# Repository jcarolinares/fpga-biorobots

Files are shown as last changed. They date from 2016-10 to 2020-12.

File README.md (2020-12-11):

# FPGA- BIOROBOTS

## Hybrid bio-inspired architecture for robots using open source FPGAs.

Animal nervous system             |  Bio-inspired robot nervous system
:-------------------------:|:-------------------------:
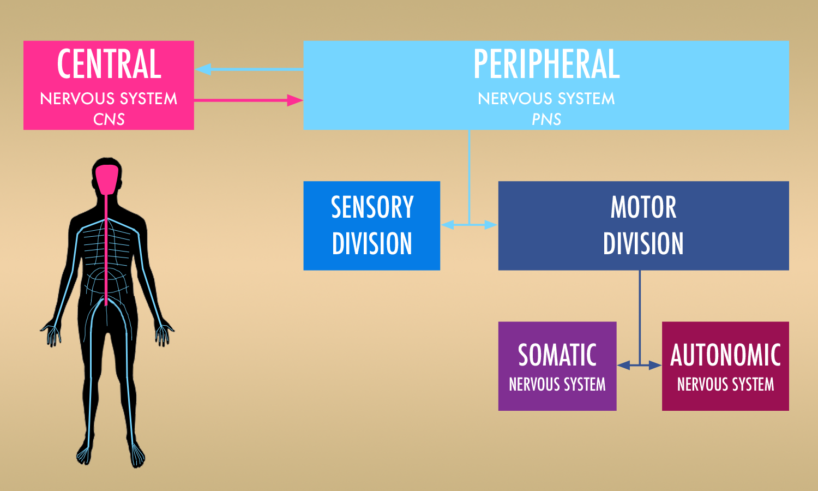
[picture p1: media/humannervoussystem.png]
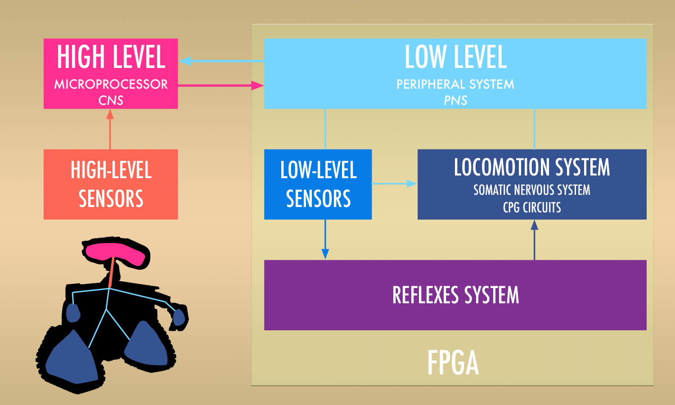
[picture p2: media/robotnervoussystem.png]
  |  

:gb: A robotic control architecture inspired in the animal nervous system that combines the use of microcomputers as the brain with the use of Open Source FPGAs as the nervous system.

Here you can find all the publications, material, robots, tools, circuits and programs developed for my master thesis work at Universidad Politécnica de Madrid.

***

:es: Repositorio con el material generado para mi trabajo de fin de Master de Robótica y Automática por la Universidad Politécnica de Madrid sobre el desarrollo de una arquitectura de control robótica híbrida y bioinspirada combinando microprocesadores y FPGAs libres.

***
## Publications

### IROS 2018 Paper

Part of this project has been published at **_2018 IEEE/RSJ International Conference on Intelligent Robots and Systems_** or **_IROS 2018_** with the title:

_"Hybrid Bio-Inspired Architecture for Walking Robots Through Central Pattern Generators Using Open Source FPGAs"_

https://ieeexplore.ieee.org/abstract/document/8594288

You can cite this article on bibtex with:

```
@inproceedings{linares2018hybrid,
  title={Hybrid bio-inspired architecture for walking robots through Central Pattern Generators using open source FPGAs},
  author={Linares, Juli{\'a}n Caro and Barrientos, Antonio and M{\'a}rquez, Enric Mayas},
  booktitle={2018 IEEE/RSJ International Conference on Intelligent Robots and Systems (IROS)},
  pages={7071--7076},
  year={2018},
  organization={IEEE}
}
```

### Master Thesis Memory

You can read and download the memory document of this Master Thesis project here:

https://github.com/jcarolinares/fpga-biorobots/blob/final-revision-cleaning/Thesis%20Memory/MasterThesis-BioInspiredrobotsOpenSourceFPGAs.pdf

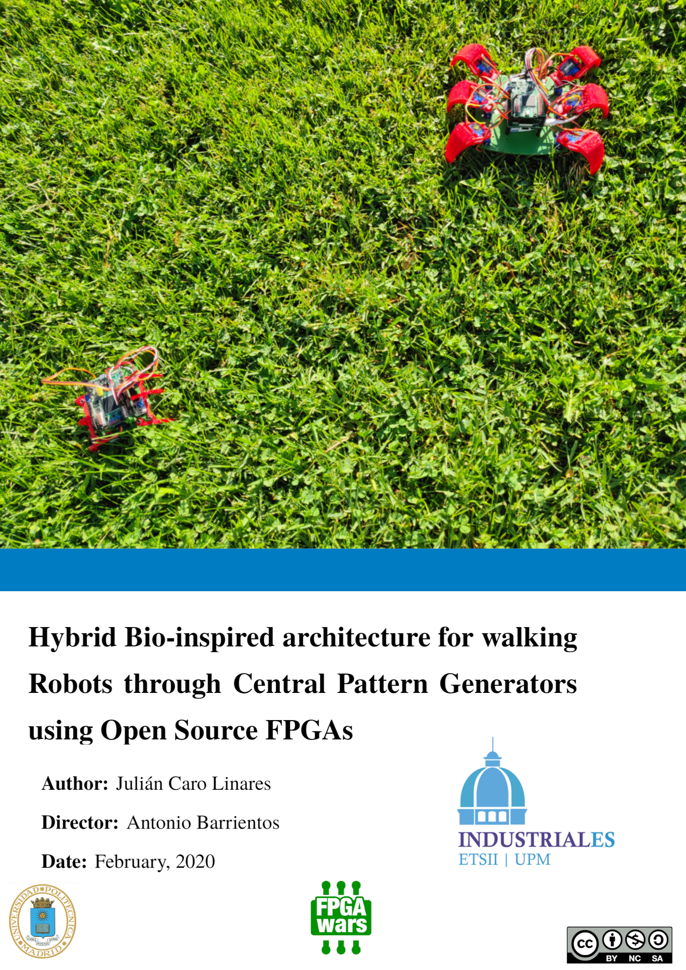
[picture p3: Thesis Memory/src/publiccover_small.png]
Master Thesis cover


You can cite this article on bibtex with:

```
@mastersthesis{fpgabiorobots2020,
  title={Hybrid bio-inspired architecture for walking robots through Central Pattern Generators using open source FPGAs},
  author={Linares, Juli{\'a}n Caro},
  school={Universidad Polit{\'e}cnica de Madrid},
  year={2020}
}
```

***

<br /><span xmlns:dct="http://purl.org/dc/terms/" property="dct:title">FPGA-Biorobots</span> by <span xmlns:cc="http://creativecommons.org/ns#" property="cc:attributionName">Julián Caro Linares</span> licensed by <a rel="license" href="http://creativecommons.org/licenses/by-sa/4.0/">Creative Commons Attribution-ShareAlike 4.0 International License</a>.<br /><br />

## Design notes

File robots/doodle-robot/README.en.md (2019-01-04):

# Doodle- Assembly instructions

  

**Read this in other languages:** :es: [Spanish](README.md)

**Some videos of Doodle**

<a href="http://www.youtube.com/watch?feature=player_embedded&v=VI5Jhr64cQY
" target="_blank">Basic video</a>
<a href="http://www.youtube.com/watch?feature=player_embedded&v=HQzxtiUjpWk
" target="_blank">Normal VS Triangular oscillators movement</a>   <a href="http://www.youtube.com/watch?feature=player_embedded&v=YqtSMF6W4vM
  " target="_blank">Line follower</a>
  <a href="http://www.youtube.com/watch?feature=player_embedded&v=JEpjGYJFocM
  " target="_blank">Fake slow motion movement</a>
  <a href="http://www.youtube.com/watch?feature=player_embedded&v=NQqp7YjglOo
  " target="_blank">Line follower using oscillators</a>
  <a href="http://www.youtube.com/watch?feature=player_embedded&v=UbCZ-bBiaz4o
  " target="_blank">Triangular oscillator VS Sine oscillators</a>
<br><br>

Here you have a step by step guide to assemble the Doodle robot. Doodle is a very simple robot and its building shouldn't take more than 30 minutes.

## Materials

### Electronic

* 1x-Icezum Alhambra, Arduino UNO or an equivalent board.

* 3x-Micro small micro servomotors of the family SG90R. In the original robot I've used ** SG92R ** servomotors. You will versions of the legs for the SG90 servomotors and SG92.

* [Optional] 2x-Lipo batteries: 3.7 V 240 mAh + Compatible charger. There are many options on the internet, an example:

  http://www.dx.com/p/502030-240mah-rechargeable-polymer-li-ion-battery-silver-227107

* [Optional] Additional sensors or servomotors. In the front part of the robot there's two general purpose holes where you can add sensors of a Educational robotis kits (Example: bq sensors) or two servomotors

### Screws and servomotors horns

You'll need **M3 and M2 screws and nuts**, also the small screws that come with the servomotors. The long of each screw is not important so you'll could build the robot using any M3 or M2 screw that you have.

* 4x-Screws M2x10

* 1x-Screw M2x15 or similar

* 8x-Screws M3x8

* 4x-Screws M3x25 [2 Optional-Battery holder]

* Screws and horns included with the servomotors.

* 1x-Double horn

* 2x-Single horn

### 3D parts

You'll need to print:

* 1x-Front left leg

* 1x-Front right leg

* 1x-Back left leg

* 1x-Back right leg

* 1x- Central leg

* 2x Leg links

* 1x base

* [Opcional] 1x- Battey holder

* [Opcional] 2x- Googly eyes

***
## Assembly step by step

**1-** Put the two servomotors in the back holes of the robot using M2x10 screws and nuts.

  

**2-** Carefully, insert the M3 nut inside each leg, depending of your 3D printer quality you'll need to push the nuts with a little pressure, even heating up the nuts a little bit

  

  **Tip:**

  It is not essential but you can put a bit of silicone at the end of the legs using a hot melt gun. Your robot will have a better adhesion to the surface.

  

**3-** Insert the single horns in each leg and attach them to the servomotors. Althought you can fix it later without problems, **is important** that at this moment you can try to put the legs on the servos in order to have an amplitude of 90 degrees backwards and forward. The position where the legs are perpenticular to the base has to be 90 degrees on your servo. You can create a simple program for this purpose. Screw the legs to the servomotors.

     

**4-** If you are going to put some sensors or additional servomotors in the front holes it's  the right time to do it. Use M3 Screws and nuts for the sensors and M2 for the servomotors.

  

  **Tip:**

  If you are going to use the battery holder, screw it only the sensors screws near the outside of the base, leave the central holes empty.

**5-** Screw the front legs in the front holes using M3 screws and nuts. Keep in mind that the leg has to turn free so don't tight it up too much. If you are going to use the battery holder, use longer screws like M3x18.

  

**6-** Screw the leg links on the legs. The bug hairs have to be at the outside . Use M3x8 and remember to let that the legs can move free.

  

**7-** Put the double horn in the central leg. Attach the leg to the servomotor keeping in mind that the 90º degrees position will be the neutral position of the leg.

  

**8.** Fit the central servomotor in the base using a long M2 screw and a nut.

  

**9-** Attach your FPGA Icezum Alhmabra or Arduino UNO board (or similar) on the columns using M3 screws.

  

  **Tip:**

  Before the board attachment

  Before placing the board, make sure that your cables pass through the central area of the robot at the rear, between the two servos.

  

**10-** Customize your robot putting a pair of googly eyes in the front.

Doodle is ready!

  

***
[Optional-Battery holder]

In the case you wish to use the battery holder you'll have to use long M3x18 screws in the step 5.



***

<br /><span xmlns:dct="http://purl.org/dc/terms/" property="dct:title">Doodle </span> by <span xmlns:cc="http://creativecommons.org/ns#" property="cc:attributionName">Julián Caro Linares</span> licensed by <a rel="license" href="http://creativecommons.org/licenses/by-sa/4.0/">Creative Commons Attribution-ShareAlike 4.0 International License</a>.<br /><br />

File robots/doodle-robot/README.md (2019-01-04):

# Doodle- Instrucciones de montaje

  

**Read this in other languages:** [English](README.en.md)

**Algunos vídeos en funcionamiento**

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

Aquí tienes una guía paso a paso para montar a Doodle. Doodle es un robot muy sencillo por lo que su montaje no debería llevarte más de media hora.

## Materiales

### Electrónica

* 1x-Icezum Alhambra, Arduino UNO o placa equivalente.

* 3x-Micro servomotores pequeños de la familia SG90R. En el robot original se han usado servomotores **SG92R** por lo que encontrarás patas para las dos versiones: SG90 y SG92R.

* [Opcional] 2x-Baterías lipo 3.7 V 240 mAh + Cargador compatible. Existen muchas baterías lipo de este tipo. Un ejemplo:

  http://www.dx.com/p/502030-240mah-rechargeable-polymer-li-ion-battery-silver-227107

* [Opcional] Sensores o servomotores adicionales. En la parte delantera del robot hay dos hendiduras donde pueden agregarse sensores de kits de robótica tipo bq zum o similares o dos servomotores.

### Tornillos y cabezales de servomotor

Necesitarás tornillos de **métrica M3 y M2** así como **los tornillos que vienen con los servomotores**. Los **tamaños** de cada tornillo **no son excesivamente importantes** por lo que podrás realizar el montaje con cualquier tornillo de las métricas M2 o M3 que tengas a mano.

* 4x-Tornillos M2x10

* 1x-Tornillo M2x15 o similar

* 8x-Tornillos M3x8

* 4x-Tornillos M3x25 [2 Opcionales-Portabaterías]

* Tornillos y cabezales incluidos con los servos.

* 1x-Cabezal doble

* 2x-Cabezal simple

### Piezas 3D

Necesitarás imprimir:

* 1x-Pata delantera izquierda

* 1x-Pata delantera derecha

* 1x-Pata trasera izquierda

* 1x-Pata trasera derecha

* 1x- Pata central

* 2x Links de patas

* 1x base

* [Opcional] 1x-Portabaterias

* [Opcional] 2x-Ojitos saltones

***
## Montaje paso a paso

**1-** Introduce los dos servomotores en su hueco de la parte trasera del robot. Atorníllalos con tornillos y tuercas M2x10

  

**2-** Con cuidado, introduce la tuerca en las patas traseras Dependiendo de tu impresora y calibración tendrás que introducir las tuercas con un poco de presión o incluso aplicando calor. Coloca también el *horn* de un solo brazo dentro de la pata, introduciéndolo a presión hasta que que su lado posterior quede dentro de la pata.

  

  **Consejo:**

  Aunque no es imprescindible,  para hacer que tu robot tenga más adhesión puedes poner un poco de silicona en sus patas utilizando una pistola de termofusible. Procura que el pegote que pegues no sea demasiado grande y quede plano sobre la pata.

  

**3-** Introduce los *horns* de un solo brazo en cada pata y coloca las patas sobre los servomotores. Aunque más tarde podrás corregirlo sin problemas, **es importante** que ahora intentes colocar las patas en los servos de forma que tengan una amplitud de movimientos de hasta 90 grados hacia atrás y chocando con la base hacia delante, siendo el ángulo 90º el perpenticular a la base. Para ello puedes incluso crear un pequeño programa donde pongas tus servos a 90º y aprovecha para atornillarlos.

     

**4-** Si vas a colocar algún sensor o servo adicional en las ranuras delanteras, es un buen momento para hacerlo. Utiliza tornillos y tuercas M3 para los sensores y tornillos y tuercas M2 para los servomotores.

  

  **Consejo:**

  En el caso de que vayas a colocar el portabaterias inferior, atornilla solo los tornillos de los sensores de la parte exterior, deja los agujeros centrales sin atornillar.     

**5-** Atornilla las patas delanteras en los agujeros de delante utilizando tornillos y tuercas M3. Recuerda que la pata debe poder girar libremente, por lo que no la aprietes demasiado . Puedes usar tornillos M3x10 o inferiores si no vas a colocar un portabaterias en la zona inferior, o utilizar tornillos M3x18 en caso afirmativo.

  

**6-** Atornilla los links o transmisores de movimiento sobre las patas. Los pelos del insecto deben quedar en la parte exterior del robot. Utiliza tornillos M3x8 y recuerda apretar bien pero permitiendo el movimiento de las patas.

  

**7-** Coloca el *horn* doble en la pata grande central. Atornilla la pata al servomotor recordando que la posición 90 grados será la posición natural de la pata, totalmente horizontal.

  

**8-** Encaja el servomotor central en la base situada en la parte delantera. Aseguralo utilizando un tornillo largo y una  tuerca M2.

  

**9-**  Coloca tu FPGA Icezum Alhambra o una placa Arduino Uno o equivalente, atornillándola con tornillos M3 en las columnas delanteras del robot.

  

  **Consejo:**

  Antes de colocar la placa procura que tus cables pasen por la zona central del robot en la parte trasera, situándose entre ambos servos.

  

**10-** Decora tu robot colocándole un par de ojitos saltones en la parte delantera.

  ¡Doodle está listo para la acción!

      

***
[Opcional-Portabaterías]

En el caso de que desees colocar el portabaterias deberás utilizar tornillos largos M3x18 o más en la zona en el paso 5 con sus respectivas tuercas en la parte inferior.



***

<br /><span xmlns:dct="http://purl.org/dc/terms/" property="dct:title">Doodle </span> por <span xmlns:cc="http://creativecommons.org/ns#" property="cc:attributionName">Julián Caro Linares</span> licensed by <a rel="license" href="http://creativecommons.org/licenses/by-sa/4.0/">Creative Commons Attribution-ShareAlike 4.0 International License</a>.<br /><br />

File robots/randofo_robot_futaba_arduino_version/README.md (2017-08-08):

# Randofo-Arduino and Futaba 3003 Version

  

  **A video of Randofo controlled with oscillators and an open source FPGA**

  <center><a href="http://www.youtube.com/watch?feature=player_embedded&v=ET-EtgHS6wI
  " target="_blank">Time to meal video</a></center><br><br>

This is Randofo. A very cool and simple robot created by Randy Sarafan (His nick is Randofo in Instructables)

You can find the original version here:

http://www.instructables.com/id/3D-Printed-Robot/

The original project uses Standar Servos from Radioshack. I created my own version of the body to use **futaba 3003 motors or similar and Arduino UNO or similar boards**

I also created a hardware control using Icestudio and the Icezum Alhambra, an open source FPGA board.

More info at: https://github.com/FPGAwars?page=1

## Materials

### Miscellaneous

* 4x Pencils

**At least two of them must have erasers**

### Electronics

* 2x-Futaba 3003 servomotors or similar

* 1x-Arduino UNO board or similar. In my case I used an Icezum Alhambra FPGA board.

* Batteries-Depends of your board and motors. But you can feed the robot using two Lipo batteries of 3.7V or a Powerbank.

### Screws

* 2x-Servo screws- The screws that comes with the servomotors.

* 12x Screws M3x12 or similar.

* 12 M3 nuts.

### 3D-Parts

* 1x-randofo_body

* 1x-gear

* 1x-back_legs

* 1x-left_leg

* 1x-right_leg

The legs and gears are easy to print but you'll probably need supports.

The body due to his form, however, will need more supports and time. If you are using Cura I recommend to change the Line Support distance to 3.6667 for a better support removement.  

***
## Assembly

I reccomend to follow the original instructions of instructables:

http://www.instructables.com/id/3D-Printed-Robot/

The only difference is the electronic part. In this version you directly have the PCB holes for Arduino UNO or similar.

***

## Programming

* In the case of an Arduino, you can use the original Arduino code. It's simple but it works!

* In the case that you are using an Icezum Alhambra FPGA board you have the hardware in the format of an Icestudio file. You can easily change the values of the roms that controls the servomotor movements using the program *oscillator_rom_generator.py*

You can download Icestudio here:

https://github.com/FPGAwars/icestudio

***

<br /><span xmlns:dct="http://purl.org/dc/terms/" property="dct:title">Randofo. A simple robot controlled with an Open Source FPGA</span> by <span xmlns:cc="http://creativecommons.org/ns#" property="cc:attributionName">Julián Caro Linares</span> licensed by <a rel="license" href="https://creativecommons.org/licenses/by-nc-sa/4.0/">Creative Commons Attribution-Non comercial-ShareAlike 4.0 International License</a>.<br /><br />

Based on <a xmlns:dct="http://purl.org/dc/terms/" href="http://www.instructables.com/id/3D-Printed-Robot/" rel="dct:source">http://www.instructables.com/id/3D-Printed-Robot/</a>

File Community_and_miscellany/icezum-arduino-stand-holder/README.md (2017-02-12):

# ICEzum-Arduino Stand holder



This is a simple Arduino and derivatives stand holder. I made two version, a piece where you can put your board in vertical or horizontal, and a piece with a inclination of 30 degrees to proudly show and use your board.

I made this model for the open source FPGA IceZum Alhambra, but is compatible with any Arduino UNO shape board.

You can find more info about the Icezum Alhambra at FPGAWars:

https://github.com/FPGAwars?page=1

=============

<br /><span xmlns:dct="http://purl.org/dc/terms/" property="dct:title">ICEzum-Arduino Stand holder</span> by <span xmlns:cc="http://creativecommons.org/ns#" property="cc:attributionName">Julián Caro Linares</span> licensed by <a rel="license" href="http://creativecommons.org/licenses/by-sa/4.0/">Creative Commons Attribution-ShareAlike 4.0 International License</a>.<br /><br />

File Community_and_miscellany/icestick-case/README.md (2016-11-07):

#ICEstick Case



Modified design based on the original of Juan Gonzalez Gomez:

<a href="https://github.com/Obijuan/3D-parts/tree/master/2015-12-23-icestick-case">https://github.com/Obijuan/3D-parts/tree/master/2015-12-23-icestick-case</a>

Changes respect the original:

- Optional screws supports out of the case.

- Slightly enlargement of some tolerances.

- <a href="https://github.com/FPGAwars?page=1">FPGAWars Logo </a>and ICEstick text added.

=============

<br /><span xmlns:dct="http://purl.org/dc/terms/" property="dct:title">ICEstick case</span> por <span xmlns:cc="http://creativecommons.org/ns#" property="cc:attributionName">Julián Caro Linares based on the design of Juan Gonzalez Gomez</span> licensed by <a rel="license" href="http://creativecommons.org/licenses/by-sa/4.0/">Creative Commons Attribution-ShareAlike 4.0 International License</a>.<br /><br />

Based on <a xmlns:dct="http://purl.org/dc/terms/" href="https://github.com/Obijuan/3D-parts/tree/master/2015-12-23-icestick-case" rel="dct:source">https://github.com/Obijuan/3D-parts/tree/master/2015-12-23-icestick-case</a>

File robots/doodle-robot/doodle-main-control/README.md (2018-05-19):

# Doodle brain

(WIP)

The main brain module or high level module of Doodle

This modules is able of create the low level circuits of the robots in and upload them to the FPGA in real time.

The brain can be excuted in a Raspberry pi 2 or 3 with apio installed.

Actually **is NOT compatible** with Raspberry zero due to Apio and an incompatibility between architectures.

## To correctly test this program you will need:

* Python 3

* Apio:

  ``` bash
  sudo pip3 install apio
  ```

* Empy:

 ``` bash
 sudo pip3 install empy
 ```
* Python 3 tk:

  ``` bash
  sudo apt-get install python3-tk
  ```

* Matplotlib:

  ``` bash
  sudo pip3 install matplotlib
  ```

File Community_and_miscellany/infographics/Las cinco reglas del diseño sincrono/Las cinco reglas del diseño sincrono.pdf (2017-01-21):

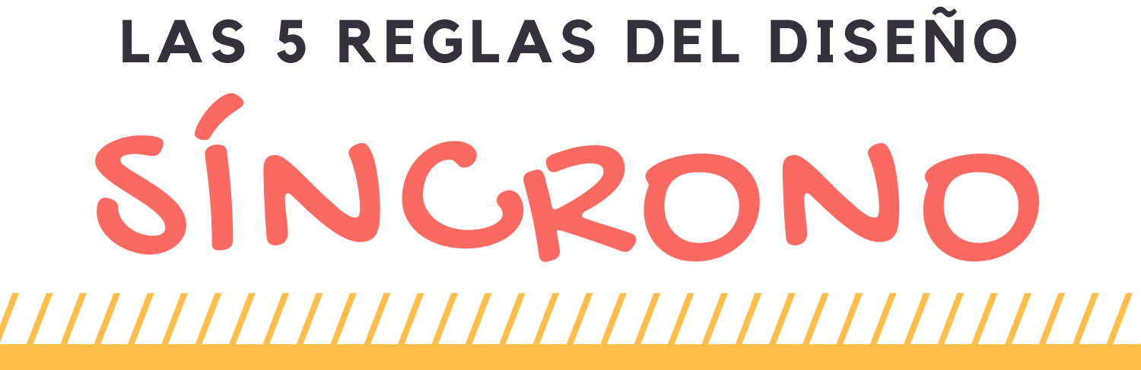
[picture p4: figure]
SÍNCRONO; LAS 5 REGLAS DEL DISEÑO

## UN ÚNICO RELOJ PARA GOBERNARLOS A TODOS

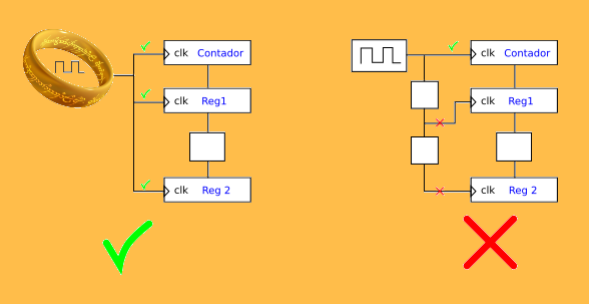
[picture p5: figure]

TODAS las entradas de reloj se deben conectar directamente a un único reloj, común a todos.

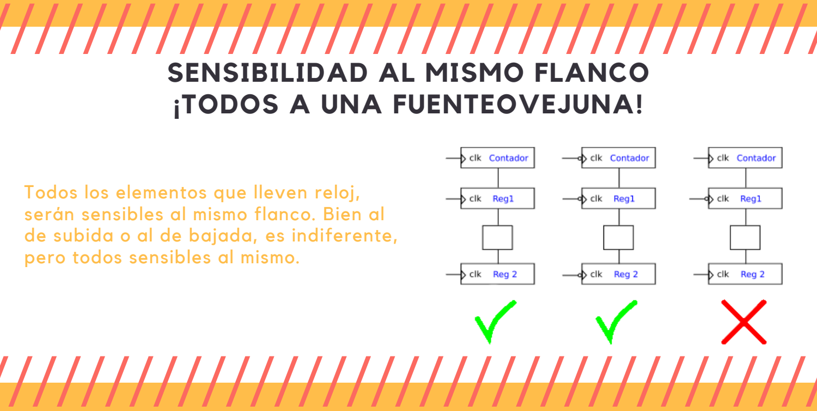
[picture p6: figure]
Todos los elementos que lleven reloj,; pero todos sensibles al mismo.; SENSIBILIDAD AL MISMO FLANCO ¡TODOS A UNA FUENTEOVEJUNA!

serán sensibles al mismo flanco. Bien al de subida o al de bajada, es indiferente,

## ANTES DE ENTRAR A UN CIRCUITO COMBINACIONAL PASE POR REGISTRO POR FAVOR

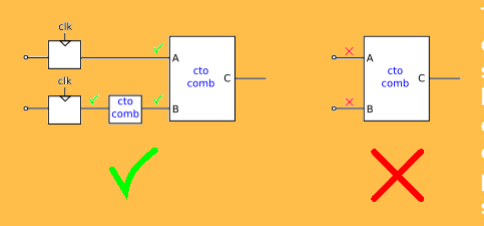
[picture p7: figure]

Todas las entradas de los circuitos combinacionales deben estar conectadas a salidas de circuitos secuenciales, sincronizadas con el reloj del sistema, o bien a otros circuitos combinacionales que cumplan esta regla. Es decir, que cualquier entrada de un circuito combinacional tiene que ser capturada antes por un registro. Las entradas que cumplen esta regla

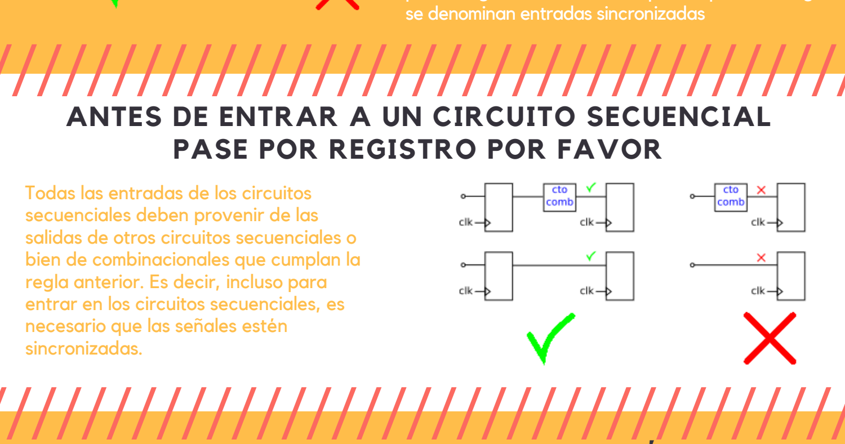
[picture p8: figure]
se denominan entradas sincronizadas; PASE POR REGISTRO POR FAVOR; Todas las entradas de los circuitos secuenciales deben provenir de las; bien de combinacionales que cumplan la regla anterior. Es decir, incluso para; necesario que las señales estén sincronizadas.

## ANTES DE ENTRAR A UN CIRCUITO SECUENCIAL

salidas de otros circuitos secuenciales o

entrar en los circuitos secuenciales, es

## SALIDAS DE UN COMBINACIONAL: SÓLO A ENTRADAS DE OTRO COMBINACIONAL, ENTRADAS SÍNCRONAS O SALIDAS DEL CIRCUITO SÍNCRONO

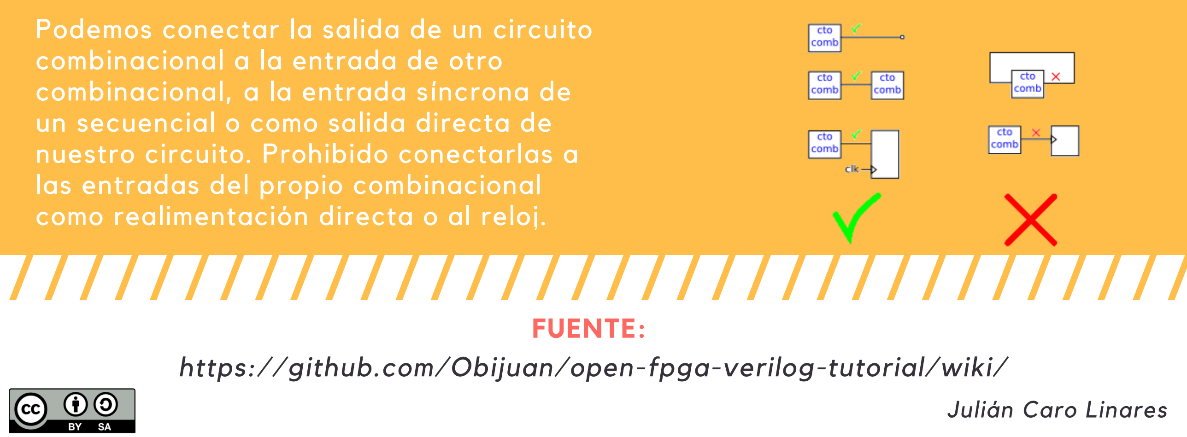
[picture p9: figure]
combinacional a la entrada de otro combinacional, a la entrada síncrona de un secuencial o como salida directa de nuestro circuito. Prohibido conectarlas a las entradas del propio combinacional como realimentación directa o al reloj.; FUENTE: https://github.com/Obijuan/open-fpga-verilog-tutorial/wiki/; Julián Caro Linares

Podemos conectar la salida de un circuito

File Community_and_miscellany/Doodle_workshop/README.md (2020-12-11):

# Doodle - Workshop

Materials of the workshop made at the [Maker Faire Oshwdem 2018.](https://oshwdem.org/2018/10/ultimos-talleres-antes-de-la-oshwdem-2018/)

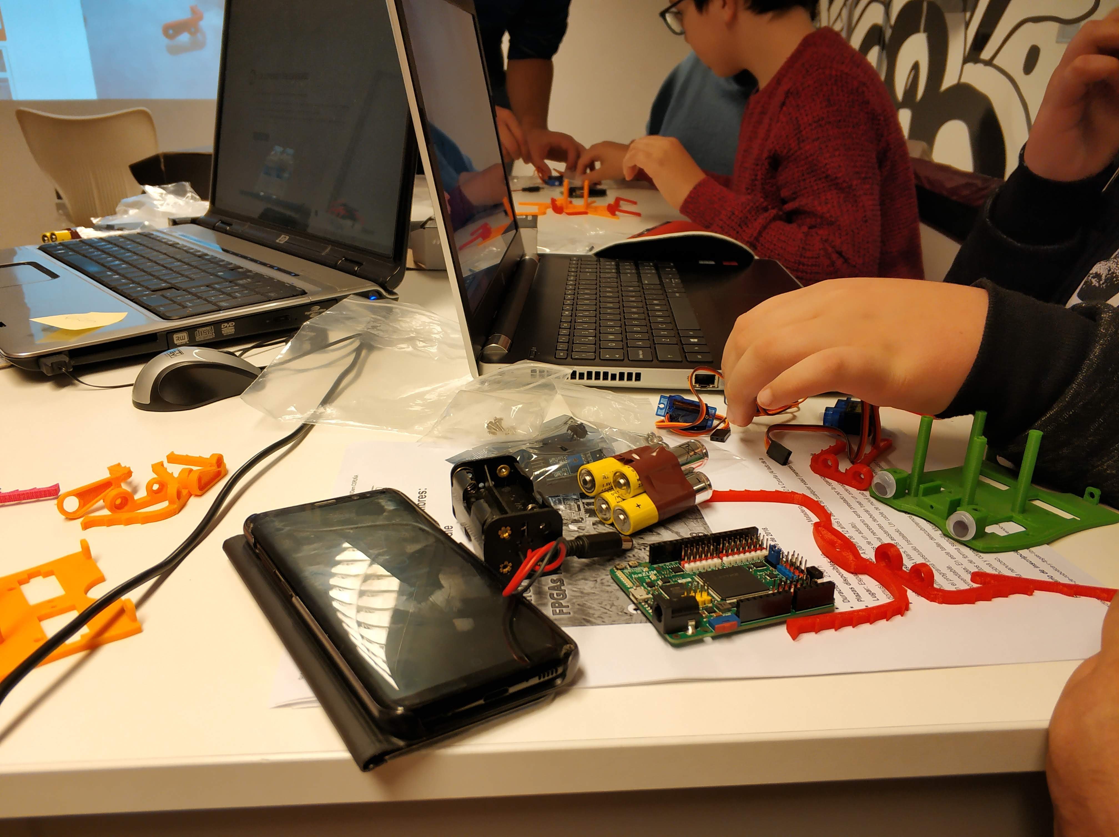
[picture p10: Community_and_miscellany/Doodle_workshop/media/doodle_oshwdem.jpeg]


The workshop, despite some problems, was so fun to do. More of the little improvements that Doodle has now were discover at this workshop.

Thank you to Nuria and Enrique and all the Oshwdem organization for their amazing help!

***

<br /><span xmlns:dct="http://purl.org/dc/terms/" property="dct:title">Doodle workshop</span> by <span xmlns:cc="http://creativecommons.org/ns#" property="cc:attributionName">Julián Caro Linares</span> licensed by <a rel="license" href="http://creativecommons.org/licenses/by-sa/4.0/">Creative Commons Attribution-ShareAlike 4.0 International License</a>.<br /><br />

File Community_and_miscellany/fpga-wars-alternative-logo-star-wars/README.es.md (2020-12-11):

# FPGA WARS: LOGO ALTERNATIVO STAR WARS

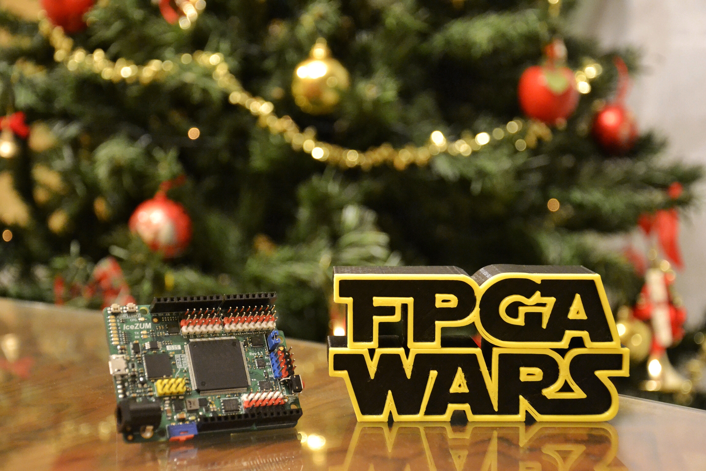
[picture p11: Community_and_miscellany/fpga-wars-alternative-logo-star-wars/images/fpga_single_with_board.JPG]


**Read this in other languages:** :gb: [English](README.md)

Repositorio con los archivos para imprimir, asi como los archivos fuente utilizados para la creación de un logo alternativo de la comunidad FPGA WARS, más información en:

- <a href="https://github.com/FPGAwars?page=1">Proyecto FPGA Wars</a>

- <a href="https://groups.google.com/forum/#!forum/fpga-wars-explorando-el-lado-libre">Comunidad FPGA Wars</a>

¡Gracias a la comunidad por su inestimable apoyo!

PD: ¿Buscas el logo de Star Wars?, pueden encontrarlo en: https://www.thingiverse.com/thing:2006957

***

<br /><span xmlns:dct="http://purl.org/dc/terms/" property="dct:title">FPGA Wars Logo Alternativo</span> por <span xmlns:cc="http://creativecommons.org/ns#" property="cc:attributionName">Julián Caro Linares</span> licensed by <a rel="license" href="http://creativecommons.org/licenses/by-sa/4.0/">Creative Commons Attribution-ShareAlike 4.0 International License</a>.<br /><br />

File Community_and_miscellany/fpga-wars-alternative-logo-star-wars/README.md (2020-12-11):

# FPGA WARS: ALTERNATIVE STAR WARS LOGO



**Read this in other languages:** :es: [Spanish](README.es.md)

Repository with the printing and source files of this alternative logo based on Star Wars for the open-source FPGA community FPGA WARS. More info at:

- <a href="https://github.com/FPGAwars?page=1">FPGA WARS project</a>

- <a href="https://groups.google.com/forum/#!forum/fpga-wars-explorando-el-lado-libre">FPGA WARS Community</a>

Thanks to the community for their unvaluable support!

PD: Are you looking for the original Star Wars logo? You can find it here: https://www.thingiverse.com/thing:2006957

***

<br /><span xmlns:dct="http://purl.org/dc/terms/" property="dct:title">FPGA Wars Alternative Logo</span> by <span xmlns:cc="http://creativecommons.org/ns#" property="cc:attributionName">Julián Caro Linares</span> licensed by <a rel="license" href="http://creativecommons.org/licenses/by-sa/4.0/">Creative Commons Attribution-ShareAlike 4.0 International License</a>.<br /><br />

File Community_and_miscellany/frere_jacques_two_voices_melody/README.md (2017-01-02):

#Frère Jacques Two voices melody

Melody created in Verilog following the tutorial example of Juan Gonzalez Gomez:

<a href="https://github.com/Obijuan/open-fpga-verilog-tutorial/wiki/Cap%C3%ADtulo-19%3A-Secuenciando-notas">https://github.com/Obijuan/open-fpga-verilog-tutorial/wiki/Cap%C3%ADtulo-19%3A-Secuenciando-notas</a>

If you have an IceZum Alhambra connect the first Buzzer to Pin 0 (119) and the second buzzer to Pin 1 (118)

If you are going to use another board, remember to change the PCF file connections.

=============

<br /><span xmlns:dct="http://purl.org/dc/terms/" property="dct:title">Frère Jacques Two voices melody</span> por <span xmlns:cc="http://creativecommons.org/ns#" property="cc:attributionName">Julián Caro Linares</span> licensed by <a rel="license" href="http://creativecommons.org/licenses/by-sa/4.0/">Creative Commons Attribution-ShareAlike 4.0 International License</a>.<br /><br />

Based on <a xmlns:dct="http://purl.org/dc/terms/" href="https://github.com/Obijuan/open-fpga-verilog-tutorial/wiki/Cap%C3%ADtulo-19%3A-Secuenciando-notas" rel="dct:source">https://github.com/Obijuan/open-fpga-verilog-tutorial/wiki/Cap%C3%ADtulo-19%3A-Secuenciando-notas</a>

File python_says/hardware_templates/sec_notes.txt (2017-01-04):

//--Fichero secnotas.v

//-- Incluir las constantes del modulo del divisor
`include "divider.vh"

//--Parametros

module secnotas(input wire clk, output reg ch_out, output reg ch_out2);

//--Notas a tocar
//--Definidas como parametros para las pruebas del testbench

parameter N0  = `DO_$octave;
parameter N1  = `RE_$octave;
parameter N2  = `MI_$octave;
parameter N3  = `FA_$octave;
parameter N4  = `SOL_$octave;
parameter N5  = `LA_$octave;
parameter N6  = `SI_$octave;
parameter N7  = `DO_$next_octave;

parameter DUR  = `T_${duration}ms;

//--Cables de salida de los canales

wire ch0, ch1, ch2,ch3,ch4,ch5,ch6,ch7;

//--Seleccion del canal del multiplexor
reg [5:0] sel=0;
reg [5:0] sel2=60;//Un compas retrasado

//-Reloj de duracion de la nota
wire clk_dur;

//--Canal 0
divider #(N0)
  CH0(
    .clk_in(clk),
    .clk_out(ch0)
  );

  //-- Canal 1
divider #(N1)
  CH1 (
      .clk_in(clk),
      .clk_out(ch1)
    );

  //-- canal 2
divider #(N2)
  CH2 (
      .clk_in(clk),
      .clk_out(ch2)
    );

//-- canal 3
divider #(N3)
  CH3 (
    .clk_in(clk),
    .clk_out(ch3)
  );

  //-- canal 4
divider #(N4)
  CH4 (
      .clk_in(clk),
      .clk_out(ch4)
);

//-- canal 5
divider #(N5)
CH5 (
    .clk_in(clk),
    .clk_out(ch5)
);

//-- canal 6
divider #(N6)
CH6 (
    .clk_in(clk),
    .clk_out(ch6)
);

//-- canal 7
divider #(N7)
CH7 (
    .clk_in(clk),
    .clk_out(ch7)
);

//multiplexor de seleccion del canal de Salida

always @*
  case (sel)
    //Frere Jacques
    0 : ch_out<=ch0;
    1:ch_out<=ch1;
    2:ch_out<=ch2;
    3:ch_out<=ch0;

    4:ch_out<=0;

    //Frere Jacques
    5:ch_out<=ch0;
    6:ch_out<=ch1;
    7:ch_out<=ch2;
    8:ch_out<=ch0;

    9:ch_out<=0;

    //Dormez-vous?
    10:ch_out<=ch2;
    11:ch_out<=ch3;
    12:ch_out<=ch4;

    13:ch_out<=0;

    //Dormez-vous?
    14:ch_out<=ch2;
    15:ch_out<=ch3;
    16:ch_out<=ch4;

    17:ch_out<=0;

    //Sonnez les matines
    18:ch_out<=ch4;
    19:ch_out<=ch5;
    20:ch_out<=ch4;
    21:ch_out<=ch3;
    22:ch_out<=ch2;
    23:ch_out<=ch0;

    24:ch_out<=0;

    //Sonnez les matines
    25:ch_out<=ch4;
    26:ch_out<=ch5;
    27:ch_out<=ch4;
    28:ch_out<=ch3;
    29:ch_out<=ch2;
    30:ch_out<=ch0;

    31:ch_out<=0;

    //Din dan don
    32:ch_out<=ch0;
    33:ch_out<=ch4;
    34:ch_out<=ch0;

    35:ch_out<=0;

    //Din dan don
    36:ch_out<=ch0;
    37:ch_out<=ch4;
    38:ch_out<=ch0;

    39:ch_out<=0;

  default: ch_out<=0;
endcase

always @*
case (sel2)
  //Frere Jacques
  0 : ch_out2<=ch0;
  1:ch_out2<=ch1;
  2:ch_out2<=ch2;
  3:ch_out2<=ch0;

  4:ch_out2<=0;

  //Frere Jacques
  5:ch_out2<=ch0;
  6:ch_out2<=ch1;
  7:ch_out2<=ch2;
  8:ch_out2<=ch0;

  9:ch_out2<=0;

  //Dormez-vous?
  10:ch_out2<=ch2;
  11:ch_out2<=ch3;
  12:ch_out2<=ch4;

  13:ch_out2<=0;

  //Dormez-vous?
  14:ch_out2<=ch2;
  15:ch_out2<=ch3;
  16:ch_out2<=ch4;

  17:ch_out2<=0;

  //Sonnez les matines
  18:ch_out2<=ch4;
  19:ch_out2<=ch5;
  20:ch_out2<=ch4;
  21:ch_out2<=ch3;
  22:ch_out2<=ch2;
  23:ch_out2<=ch0;

  24:ch_out2<=0;

  //Sonnez les matines
  25:ch_out2<=ch4;
  26:ch_out2<=ch5;
  27:ch_out2<=ch4;
  28:ch_out2<=ch3;
  29:ch_out2<=ch2;
  30:ch_out2<=ch0;

  31:ch_out2<=0;

  //Din dan don
  32:ch_out2<=ch0;
  33:ch_out2<=ch4;
  34:ch_out2<=ch0;

  35:ch_out2<=0;

  //Din dan don
  36:ch_out2<=ch0;
  37:ch_out2<=ch4;
  38:ch_out2<=ch0;

  39:ch_out2<=0;

default: ch_out2<=0;
endcase

always @(posedge clk_dur)
  begin
  sel<=sel+1;
  sel2<=sel2+1;
  end

divider #(DUR)
  TIMER0(
    .clk_in(clk),
    .clk_out(clk_dur)
    );

endmodule

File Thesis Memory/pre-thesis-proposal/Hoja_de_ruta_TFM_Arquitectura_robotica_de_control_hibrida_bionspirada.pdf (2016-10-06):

1

DEPARTAMENTO DE AUTOMÁTICA,

### INGENIERÍA ELÉCTRICA Y ELECTRÓNICA E INFORMÁTICA INDUSTRIAL

### CENTRO DE AUTOMÁTICA Y ROBÓTICA (CAR-UPM-CSIC)

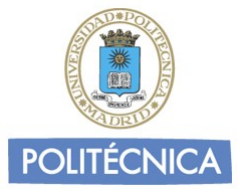
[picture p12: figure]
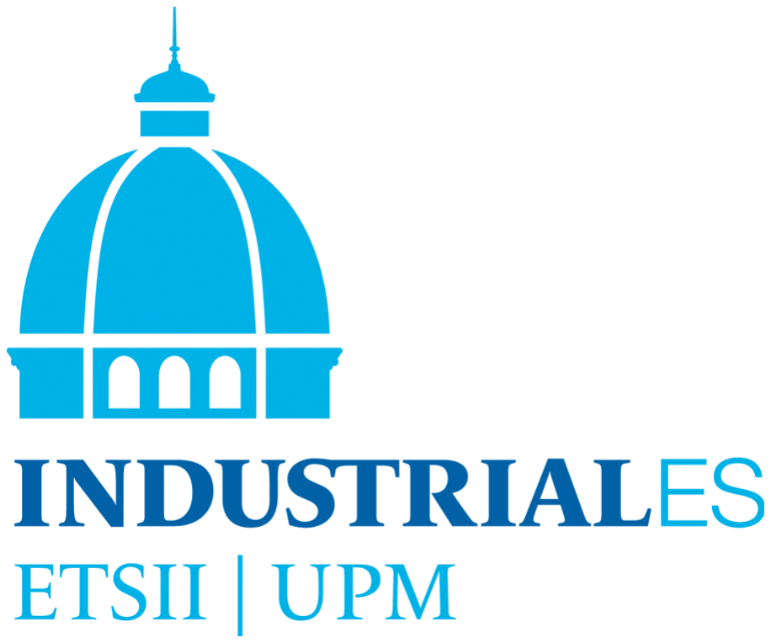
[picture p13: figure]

# MASTER UNIVERSITARIO EN AUTOMATICA Y ROBOTICA

# AVANCES

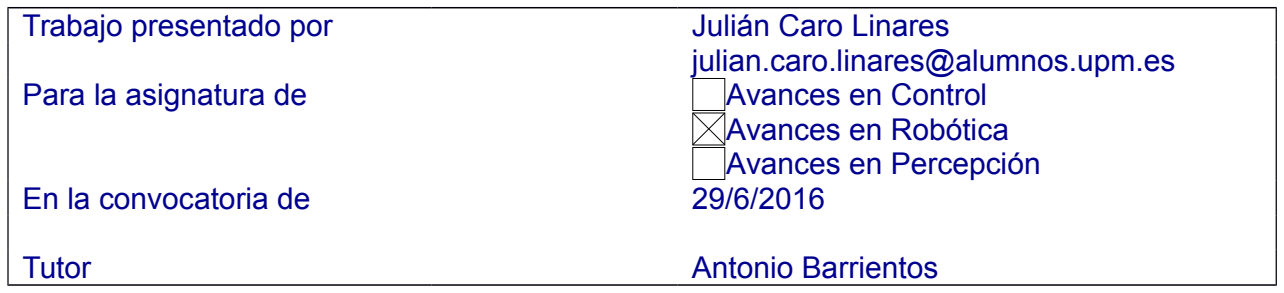
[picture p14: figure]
julian.caro.linares@alumnos.upm.es; Avances en Robótica Avances en Percepción; En la convocatoria de; Tutor; Antonio Barrientos

Trabajo presentado por | Julián Caro Linares
Para la asignatura de | Avances en Control

# TITULO Desarrollo de una arquitectura de control híbrida bioinspirada para su aplicación en robots caminantes

´

# Indice general

1. Hipótesis y objetivos | 1
2. Estado del arte | 4
3. Propuesta de validación de hipótesis | 7
4. Método de evaluación | 12
4.1. Búsqueda de soluciones de locomoción en la Biorrobótica actual . . . | 12
4.4. Mejora de la locomoción y otros sistemas mediante aprendizaje . . . . | 14
5. Conclusiones | 15
Bibliografía | 16

i

# Capítulo 1

# Hipótesis y objetivos

El presente trabajo de Avances en Robótica se plantea como una primera fase exploratoria del trabajo de fin de Máster a realizar. A continuación se plantearán las distintas hipótesis y objetivos que servirán como base para la consecución del trabajo de fin de Máster que se está desarrollando.

## 1.1. Hipótesis

El uso de las estructuras y sistemas de control actuales ha supuesto un gran avance en el campo de la robótica. Por primera vez, y a pesar de las evidentes limitaciones, los robots son capaces de detectar su entorno con una gran variedad de sensores y navegar por él resolviendo distintas tareas.
Sin embargo, el uso de ruedas, un invento meramente humano, nos está limitando. Con el auge de la robótica de servicio estas han demostrado ser, en muchas ocasiones, insuficientes. Los robots de servicios deben moverse en entornos creados y pensados para seres humanos. Esto implica espacios pequeños llenos de obstáculos, como el interior de edificios, utilización de elementos del día a día, como sillas o mesas e, incluso, el uso de herramientas pensadas para un ser humano por parte del robot. Los robots con ruedas tienen, por tanto, problemas similares a los de las personas con movilidad reducida. Por este motivo se están desarrollando cada vez más robots con piernas y de aspecto humanoide.
Un caso en el que se hizo patente la necesidad de robots más flexibles fue el desastre de la central nuclear de Fukushima [1]. La gran cantidad de escombros, escaleras, y la necesidad de accionar elementos pensados para los humanos tales como válvulas, enchufes o simples pomos de puertas, sumados al gran problema de los elevados niveles de radiación, supusieron que un robot tras otro llevaran a cabo sus tareas de forma muy limitada antes de que la radiación acabará con sus circuitos. De esta necesidad surgieron competiciones como el DARPA Robotics Challenge [2]. A pesar del gran esfuerzo por parte de empresas y universidades, observando esta competición queda patente las limitaciones de la robótica actual, donde los robots, casi todos bípedos debido a la inclinación natural de crear robots similares a los humanos para moverse por entornos humanos, necesitan de un sistema de control excepcional para el control

1

CAPÍTULO 1. HIPOTESIS Y OBJETIVOS ´ | 2

de sus articulaciones así como el constante control por parte de un ser humano. Los robots humanoides, aún con la ventaja de su gran flexibilidad, son costosos, inestables y, actualmente, poco útiles en entornos reales.
Por este motivo cada vez más instituciones optan por ofrecer soluciones alternativas a dichos problemas, muchas de ellas inspiradas en la naturaleza. Así un robot serpiente puede ser de gran utilidad en labores de rescate o exploración de tuberías como las de los reactores de Fukushima [3]. Un robot cuadrípedo puede servir de mula de carga del siglo XXI para cubrir grandes distancias en terreno abierto [4] o pequeños robots, inspirados en el comportamiento de los insectos, pueden actuar como un enjambre para la consecución de distintos objetivos [5].

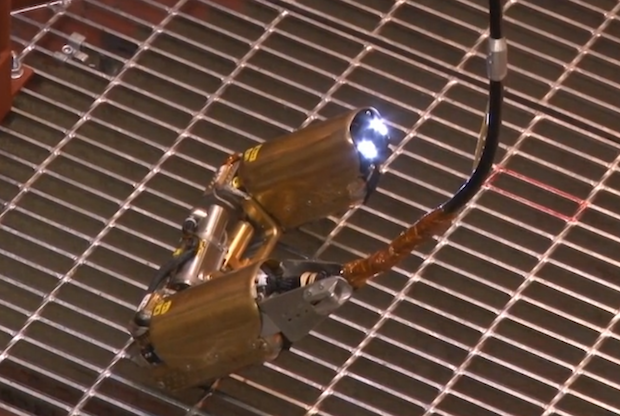
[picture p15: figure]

Figura 1.1: Serpiente robótica creada por la compañía TEPCO. A pesar de estar diseñado a propósito para la tarea, el robot quedó finalmente atascado en las tuberías del reactor de la central nuclear de Fukushima.

El ser humano ha mirado siempre a la naturaleza en busca de inspiración, bien para adaptarla a sus necesidades, bien para imitarla y aprender de ella. La robótica actual, al igual que otras materias, está fuertemente limitada por la especialización de su propio campo de estudio, en el que cada vez son más necesarios conocimientos de neurología, biología u otros.
La hipótesis de este proyecto plantea para el sistema de control de la marcha de un robot con patas, el uso de un sistema híbrido bioinspirado en el binomio Cerebro-Sistema nervioso periférico (SNP), presentando una alternativa a la aplicación del control de bajo nivel mediante la utilización de circuitos electrónicos implementados en una FPGA en vez de un microprocesador. Todo ello con el objetivo de plantear nuevas soluciones para hacer más abordable la locomoción y sensorización en la robótica actual.

## 1.2. Objetivos

Para trabajar en el desarrollo y validación de la hipótesis planteada, se establecen los siguientes objetivos:

Desarrollar una estructura de control Alto nivel-Bajo nivel: en robots donde el alto nivel sea gobernado por un microprocesador que envíe ordenes de

CAPÍTULO 1. HIPOTESIS Y OBJETIVOS ´ | 3

alto nivel a un sistema de bajo nivel y alta velocidad de respuesta. Para ello el bajo nivel puede ser realizado mediante circuitos básicos implementados en una FPGA o similares para las tareas básicas de locomoción. De esta forma se libera tiempo de procesamiento para que el alto nivel pueda especializarse en el tratamiento de información, aprendizaje y toma de decisiones.

Búsqueda de soluciones robóticas bioinspiradas: al ser un sistema fuertemente inspirado en la naturaleza, se hace necesario realizar una visión global del estado del arte de este campo de estudio.

Uso de FPGAs en robots: con la utilización de FPGAs para las órdenes de bajo nivel, surge la necesidad de plantear una visión general de su uso en la robótica actual, poniendo especial hincapié en el desarrollo y uso de FPGAs Open Source [6].

Justificación y uso: analizar los pros y contras de este tipo de control frente a otras estructuras convencionales para llegar a conclusiones sobre en qué casos puede o no suponer una ventaja para el desarrollo en un robot. Para ello se realizarán distintas pruebas en robots sencillos con el objetivo de analizar dichas ventajas e inconvenientes.

Robot prototipo: construir un prototipo de robot cuya locomoción sea modular, escalable, y a ser posible bioinspirada. El objetivo es demostrar cómo la utilización de esta estructura puede suponer una seria ventaja en la utilización de robots con sistemas de locomoción en los que el uso de múltiples grados de libertad de forma simultánea o sensorización sea un punto crítico en su desarrollo.

Implementación de CPGs: utilizar un modelo de Central Pattern Generator básico implementado en una FPGA para controlar los movimientos de un robot con el objetivo de aproximarse a una locomoción animal para analizar las ventajas de estas frente a otros sistemas de locomoción. Para ello deberán establecerse una serie de criterios o índices que permitan comparar y analizar dichas ventajas e inconvenientes mediante la realización de experimentos con diferentes arquitecturas de control,

Implementación de otros mecanismos bionspirados: explorar otros posibles campos en los que se pueda aplicar el sistema de control planteado, como la percepción del entorno del robot u otros buscando su equivalente al de la locomoción robótica y los CPG dentro de dichos campos.

Mejora de la locomoción y otros sistemas mediante aprendizaje: experimentación con sistemas de aprendizaje que mejoren, casi en tiempo real, la locomoción del robot. Para ello el sistema de alto nivel puede implementar programas de Machine learning que modifiquen los circuitos, y por tanto los sistemas de locomoción u otros, del sistema de bajo nivel.

# Capítulo 2

# Estado del arte

En este capítulo se plantea el estado del arte de la biorrobótica actual. Los sistemas más estudiados actualmente y sus posibles aplicaciones.

## 2.1. Biorrobótica

El ser humano es una especie animal muy especial. Si tenemos en cuenta la teoría de la evolución de las especies de Charles Darwin, y sus posteriores desarrollos, llegamos a la conclusión de que la evolución en el planeta Tierra ha sido provocada por la selección natural y, por tanto, la capacidad de cada individuo de adaptarse al medio que le rodea, por lo que la flexibilidad ante el cambio ha sido y es un aspecto fundamental en la evolución[7].

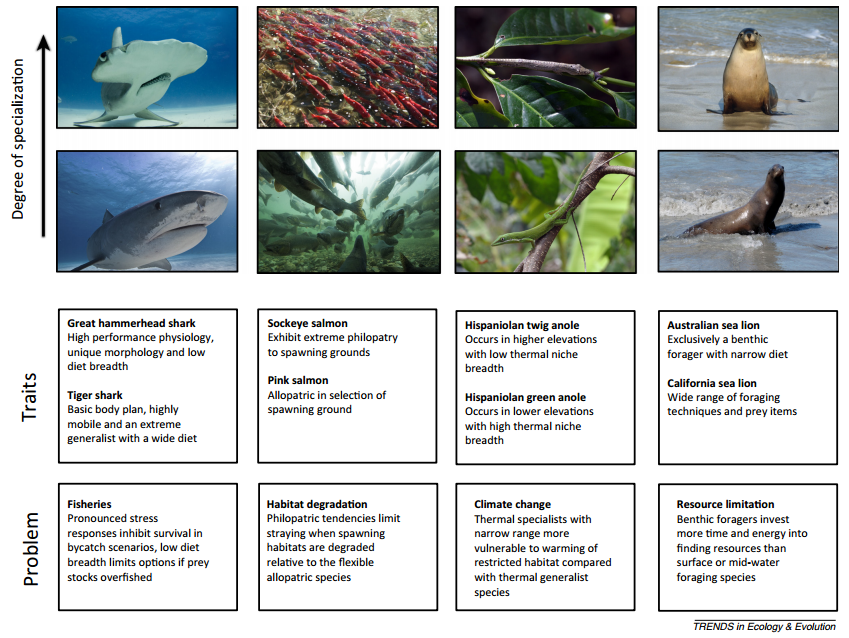
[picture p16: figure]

Figura 2.1: Ejemplo expuesto en el artículo [7] donde se muestran especies de animales con un alto grado de especialización a su medio y los posibles riesgos que ello conlleva.

Sin embargo, la peculiaridad de la evolución del homo sapiens sapiens no reside en su capacidad fisiológica ante el cambio. El ser humano no adapta su cuerpo a un nuevo medio, sino que crea herramientas, conforma y modifica el propio medio para su propio beneficio, muchas veces inspirándose en él. En ese sentido, y dejando de lado la evidente sobreexplotación del medio, el ser humano es un animal que, gracias

4

CAPÍTULO 2. ESTADO DEL ARTE | 5

a su intelecto y su capacidad de crear herramientas, es capaz de vivir en los ambientes más extremos del planeta e, incluso, fuera de él.
El campo de la biorrobótica no es más que una consecuencia directa de nuestra forma de ver el mundo. En pleno siglo XXI, en el que siglos de estudio aportan soluciones a prácticamente cualquier problema, aún nos encontramos con limitaciones de todo tipo que frenan nuestro desarrollo. Es en esos momentos cuando los seres humanos miramos a la naturaleza en busca de inspiración. Cada especie pasada y actual es la consecuencia de miles de años de selección natural, mutaciones, perfeccionamiento y adaptación al medio y cada problemática que éste presenta. Parece por tanto razonable tratar de adaptar soluciones naturales a campos de estudio tan artificiales como el de la robótica con el razonamiento de que, si funciona en la naturaleza, es una solución de calidad.
Así pues la Biorrobótica es el campo de estudio que trata sobre la construcción de robots biológicamente inspirados, ya sea en su diseño, mecánica, locomoción, actuadores y sensores o sistemas de control. La Biorrobótica es un campo de estudio que no solo se inspira en la naturaleza para su aplicación en el campo de la robótica, sino que también puede ser de gran utilidad para ampliar y facilitar la investigación en campos de estudio como la Biología y la Neurología. Tal es el caso del robot salamandra creado por Auke Jan Ijspeert et al [8] cuyo creación y uso tuvieron como principal objetivo el crear una plataforma donde se pudiera poner a prueba la hipótesis del modelo locomotor de la salamandra real basado en la estructura de CPGs [9].

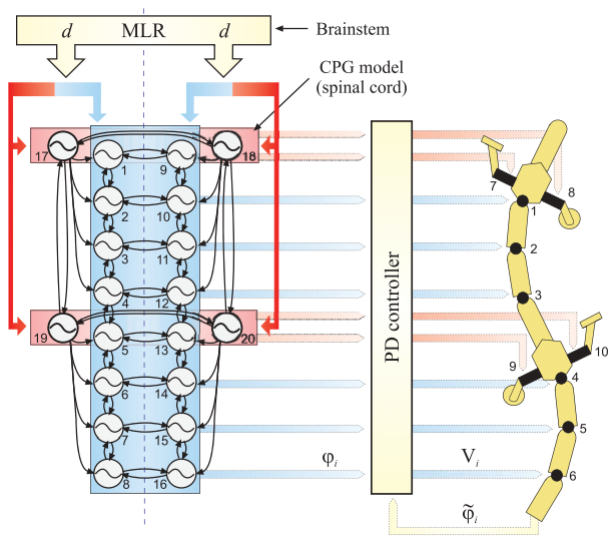
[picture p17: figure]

Figura 2.2: Modelo de locomoción de una salamandra junto a su prototipo robótico [8]. El modelo se basa en movimientos oscilatorios generados por las estructuras de control conocidas como Central Pattern Generator o CPG.

Otro ejemplo notable en el que el comportamiento de los animales inspira un desarrollo robótico es la biomecánica con la que se pretende imitar aspectos mecánicos sacados de la naturaleza para, generalmente, conseguir locomociones más estables y eficientes. Un ejemplo de ello es el pequeño robot Cheetah-Cub [10] basado en la mecánica de locomoción de los gatos y otros felinos y cuya locomoción se basa en la estructura de un pantógrafo, siendo un sistema capaz de autoestabilizarse, aún en bucle abierto, ante pequeñas perturbaciones u obstáculos, gracias a su mecánica bionspirada[11]. En la misma línea está el robot MIT Cheetah inspirado en la forma

CAPÍTULO 2. ESTADO DEL ARTE | 6

y locomoción del leopardo y que es capaz de realizar saltos de obstáculos de distintas alturas gracias a un sistema laser y la excelente configuración de sus patas [12].
Una de las empresas que más aprovecha la inspiración animal en el desarrollo de sus robots es la empresa alemana Festo. Festo ha creado una gran cantidad de robots bionspirados tanto en forma como en características. Ejemplos son su robot canguro
[13] capaz de moverse al igual que su homónimo y de recuperar parte de la energía del anterior salto para el siguiente. Este tipo de robots que imitan la locomoción de animales terrestres, aparte de la mejora de nuestro conocimiento biomecánico, tienen aplicaciones en su uso sobre terrenos abruptos o, incluso, como bestias de carga, como sucede con AlphaDog de Boston Dynamics [14].
El uso de la biorrobótica permite también afrontar con éxito locomociones en entornos en los que la mecánica tradicional necesita cambiar su planteamiento. Un ejemplo es en el vuelo, donde podemos encontrar ejemplos bionspirados como el del robot murciélago creado por el CAR [15], o la libélula y la gaviota de Festo [16] [17]. Este tipo de robots pueden ser utilizados para labores de vigilancia o control de un medio natural, como la monitorización de incendios, contaminación, u otros aspectos en parques naturales, siendo su impacto ambiental mucho menor frente a otras alternativas.
El uso de robots bionspirados en ambientes acuáticos, aún en un desarrollo muy temprano, presenta importantes aplicaciones en un medio donde las reglas de la locomoción cambian. Son buenos ejemplos robots como la medusa Aquajelly [18] o los peces de Maurizio Porfiri et Al [19]. Otro caso es el robot híbrido creado por la UPM
[20] y que pasa de un robot clásico marino a una locomoción animal para explorar el fondo oceánico. Estos robots presentan grandes ventajas a la hora de explorar medios marinos, siendo una gran herramienta en el campo de la biología marina al imitar a animales propios del medio.
Pero el campo de la biomimética no es el único que se utiliza en la biorrobótica. Aparte de la imitación de cuerpos y locomociones animales, existen otros campos como el estudio de comportamientos emergentes a través de la creación de enjambres de robots que, con una serie de reglas básicas, son capaces de realizar tareas tales como la auto-organización del enjambre, tal como hace el robot Kilobot [21], o la imitación de la comunicación química de las hormigas para crear una ruta entre la comida y el hormiguero [22].
Por último, destaca también la imitación y estudio de las estructuras de control en la locomoción de robots. Suelen basarse en el concepto de CPG o Central Pattern Generator un concepto del campo de la neurobiología que explica cómo un conjunto de células interconectadas son capaces de generar patrones de señal rítmicos y oscilatorios en los que se basan muchos movimientos animales. Debido a la complejidad de los sistemas nerviosos animales, estos CPGs se implementan basándose en animales con sistemas simples tales como la lamprea [23] o la ya mencionada salamandra [8]. Este campo de estudio puede resultar fundamental para entender la forma en la que la naturaleza controla la locomoción de forma eficaz y eficiente, aplicando esos mismos principios a sistemas de control artificiales.

# Capítulo 3

# Propuesta de validación de hipótesis

Como se mencionó en el apartado 1, la principal hipótesis del TFM es la experimentación en la creación de un sistema híbrido de control bioinspirado como alternativa en la creación de los robots actuales. Este sistema de control estaría fuertemente basado en sistemas de control estudiados dentro de la locomoción y percepción de su medio en especies animales.

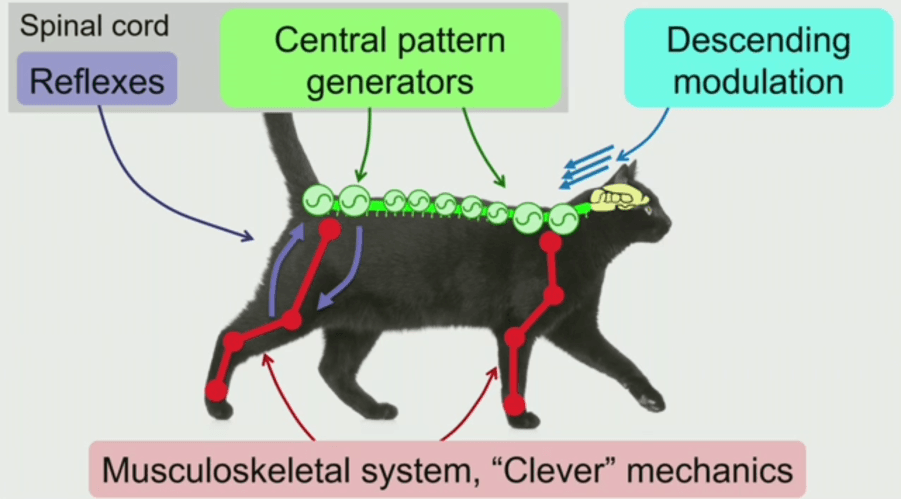
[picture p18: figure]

Figura 3.1: Estructura básica de la locomoción animal planteada por A.Spröwitz [10] y basada en CPGs (apartado 2.1)

El sistema trataría de imitar el binomio de control órdenes de alto nivel-órdenes de bajo nivel presente en la naturaleza, estando formado por un control de alto nivel y uno de bajo nivel. A continuación se presentan ambos sistemas y las distintas opciones para la implementación de los mismos.

## 3.1. Sistema de alto nivel

El sistema de alto nivel se encargaría del procesamiento complejo de la información recibida por los sensores, la toma de decisiones y la planificación de los próximos movimientos del sistema de forma general. Para ello el sistema de alto nivel tendría como base un microprocesador. Debido a los recursos disponibles, la facilidad de

7

CAPÍTULO 3. PROPUESTA DE VALIDACION DE HIP ´ | OTESIS ´ | 8

manejo y el deseo del desarrollo de robots lo más pequeños posibles, se barajan dos soluciones técnicas a implementar:

### 3.1.1. Microcontrolador

El uso de un microcontrolador que administre las entradas y salidas de alto nivel para comunicarse con el sistema de bajo nivel u otros sistemas se plantea como una opción interesante a utilizar. Existen numerosos microcontroladores en el mercado que, por su configuración, pueden ser de gran utilidad en el desarrollo de sistemas robóticos con un gran rango de recursos y precios. Dado el deseo del trabajo de experimentar, diseñar e implementar el sistema sobre robots reales, se plantearía el uso de microcontroladores Open Source como aquellos de la familia Arduino UNO y similares.
Los microcontroladores Open Source fueron creados con el deseo de facilitar las prácticas de electrónica y automatización en universidades, así como ofrecer un dispositivo barato, fácil y práctico para otros campos culturales como el del arte contemporáneo. En la actualidad es ampliamente usado como herramienta educativa en escuelas, institutos, universidades y otras instituciones. También tiene una gran presencia en la electrónica y robótica a nivel de hobby, destacando en el movimiento Maker que busca la creación de pequeños automatismos y soluciones caseras para cualquier necesidad actual. Derivado de este movimiento, este tipo de microcontroladores Open Source son ampliamente usados en la creación de productos basados en el internet de la cosas o IoT por parte de numerosas Startups que se financian a través de campañas de micromecenazgo.
Dentro del ámbito de la investigación universitaria, los microcontroladores Open source representan una primera aproximación al problema a investigar razonable, siendo en muchas ocasiones suficiente para el objetivo perseguido. Son por tanto, una herramienta de prototipado rápido que permite, a un costo muy pequeño, experimentar con distintos caminos antes de emprender el camino y estudio hacia prototipos de mayor complejidad y coste.
La mayoría de microcontroladores basados en la familia Arduino utilizan un microprocesador como el ATMEGA328P o similares. Estos microcontroladores, si bien no son muy potentes, son suficientes para la realización de numerosos sistemas básicos de automatización y la creación y control de pequeños robots. Además poseen una gran comunidad y documentación detrás, existiendo placas adicionales o shields para practicamente cualquier finalidad, por lo que son una gran opción de cara al desarrollo del sistema. La mayoría de estos sistemas pueden ser programados en lenguaje Arduino, un lenguaje simplificado de C y C++ y basado en Processing, o en otros muchos lenguajes, tales como C y C++, Java, Python o herramientas de simulación matemática y de control como Matlab y Simulink.
Sin embargo poseen importantes limitaciones en su memoria, velocidad de procesamiento y resto de capacidades. Estos microcontroladores son generalmente usados como un único sistema de control que combina el alto y bajo nivel, debido a su baja velocidad de procesamiento, implica importantes limitaciones en la sensorización y actuación de un sistema robótico, siendo muy difícil la creación de un sistema en el

CAPÍTULO 3. PROPUESTA DE VALIDACION DE HIP ´ | OTESIS ´ | 9

que se den procesos cuasi simultáneos sin aumentar el número de procesadores. Dado que el objetivo del proyecto es que el sistema de alto nivel se encargue solo de procesar información de alto nivel como la toma de decisiones, así como el cambio y evolución en tiempo real del sistema de bajo nivel, se plantea el uso de microcontroladores solo como sustituto esporádico del control de alto nivel para la experimentación con la estructura de bajo nivel, pero no como sistema principal y final del control de alto nivel.

### 3.1.2. Microordenador

Dado las limitaciones en el uso de microcontroladores como Arduino se plantea el uso de microordenadores como sistema de control de alto nivel. Debido a la ley de Moore, la electrónica ha experimentando un crecimiento periódico en la capacidad de los microprocesadores. Esto, aparte del acceso a herramientas de procesamiento cada vez más potentes, ha permitido el abaratamiento progresivo de los microprocesadores anteriores teniendo acceso a ordenadores cada vez más baratos con la misma potencia. En los últimos años, y siguiendo el movimiento de hardware libre iniciado por Arduino han surgido distintos microordenadores de muy bajo coste entre los que destacan por su gran difusión el microordenador Raspberry Pi. En sus últimos modelos, este ordenador dispone de características interesantes como 1 GB de RAM, una velocidad de CPU considerable y protocolos de comunicación tales como bluetooth y wifi. Aparte de varios puertos USB, una salida HDMI y una de audio tipo jack, el dispositivo suele disponer de pines GPIO para la comunicación con otros aparatos, lo que lo hace ideal como sistema de alto nivel en aplicaciones de IoT, robótica y otros. Su pequeño tamaño y bajo coste influyen también en su elección, ya que permiten el desarrollo de prototipos más baratos y pequeños, existiendo incluso modelos como Raspberry pi Zero o C.H.I.P capaces de ser integrados en espacios muy pequeños.
Pero la característica más importante que hace de un microordenador una gran elección es el software. Mientras que con el uso de un microcontrolador solo tenemos un sistema programable de entradas y salidas, con un microordenador disponemos de un sistema operativo completo. Los microordenadores actuales suelen utilizar distribuciones de Linux, generalmente basadas en Debian y optimizadas para estos. En los últimos tiempos también se han añadido otros SO como windows 10. Disponer de un sistema operativo basado en Linux ofrece grandes ventajas. Desde la creación de una plataforma de visión por computador simple utilizando Opencv, a infinitas opciones de programación en el alto nivel, conexión a internet y acceso al sistema mediante FTP, no siendo necesario conectar físicamente el robot a ningún monitor. Además, y basándose en los objetivos deseables de crear un sistema de alto nivel capaz de cambiar en tiempo real la configuración o programación del sistema de bajo nivel, el uso de un microordenador se presenta como una gran opción.

CAPÍTULO 3. PROPUESTA DE VALIDACION DE HIP ´ | OTESIS ´ | 10

## 3.2. Sistema de bajo nivel

Junto al alto nivel, el objetivo del trabajo es utilizar una estructura de bajo nivel que sea la principal responsable de la locomoción, sensorización y control en detalle del robot. Si tenemos un control de bajo nivel directamente responsable de las órdenes de locomoción más detalladas y complejas, obtendremos un robot cuyo alto nivel podrá procesar más información y llevar a cabo más tareas de toma de decisiones y aprendizaje.
Como elemento que conformará el bajo nivel se plantea, en vez del tradicional uso de un microprocesador, la utilización de circuitos electrónicos simples para experimentar con la generación de locomociones simples, sensorización e, incluso, reflejos. Puede pensarse que la realización de circuitos electrónicos personalizados como sistema de bajo nivel supone una seria desventaja respecto al uso de un microprocesador, ya que parece necesario montar sistemas electrónicos a mano o PCBs personalizadas, con un gran coste de dinero, tiempo y habilidades.
Sin embargo el trabajo no pretende la creación de circuitos electrónicos tradicionales, si no la implementación de estos en una FPGA. Las FPGAs se han utilizado tradicionalmente para el testeo de circuitos electrónicos antes de su producción en masa, o para la experimentación de nuevos tipos de circuitos. Son capaces de almacenar (de forma volátil) numerosos circuitos dependiendo de su capacidad y, al ser circuitos físicos y no de programación mediante una serie de órdenes que se ejecutan de una en una, su velocidad y capacidad de respuesta es muy superior al de un microprocesador. Esto, que en un robot simple no supone una diferencia significativa de rendimiento frente al trabajo que supone la implementación en una FPGA, puede cambiar cuando hablamos de sistemas modulares, con un gran número de grados de libertad que tengan que ser accionados al mismo tiempo, o cuando se desea la respuesta a gran velocidad del robot ante estímulos, siendo una alternativa interesante en la implementación de reflejos en un robot.
Por otra parte, el uso de FPGAs para la implementación de circuitos simples como sistema de bajo nivel, permite aproximarse más aún al modelo de control animal previamente comentado, donde gran parte del trabajo se realiza mediante señales rítmicas periódicas (CPG) generadas directamente por el sistema nervioso central y activadas por el cerebro mediante una simple orden de alto nivel. El uso de una FPGA permite que este trabajo, en un futuro, pueda implementar un sistema de CPG simple con el objetivo de acercarse más aún a una locomoción bioinspirada. Tradicionalmente, las FPGAs se han movido en el terreno de los grandes fabricantes, siendo propietarias y dependientes de softwares específicos y relativamente caros. Sin embargo, en el último año y medio, ha surgido un movimiento que, similar al observado en el campo de los microprocesadores y la impresión 3D, ha empezado a generar FPGAs Open Source.
Este nuevo movimiento surgió en 2015 con el proyecto IceStorm [24] liderado por Clifford Wolf y que consiguió generar un bitstream a partir de un código en Verilog mediante herramientas libres. Aun siendo un proyecto libre muy nuevo, solo compatible con dos modelos de FPGAs actualmente (Lattice modelos: HX1K-TQ144 y HX8K-CT256) y con ciertas limitaciones en su software, como no poder programar

CAPÍTULO 3. PROPUESTA DE VALIDACION DE HIP ´ | OTESIS ´ | 11

actualmente en VHDL, si no solo en Verilog, el uso de FPGAs libres revela un gran potencial, desde una mayor autonomía por parte del desarrollador, a usos no previstos por el fabricante, creación de una comunidad que comparta y mejore el conocimiento e, incluso, la creación de repositorios de circuitos de hardware libre fácilmente reconfigurables.
Siguiendo este camino, Juan González Gómez y Jesús Arroyo han tomado como base el proyecto IceStorm y han iniciado el proyecto FPGAwars [6], del que cabe destacar la creación de una placa de desarrollo denominada IceZum Alhambra.

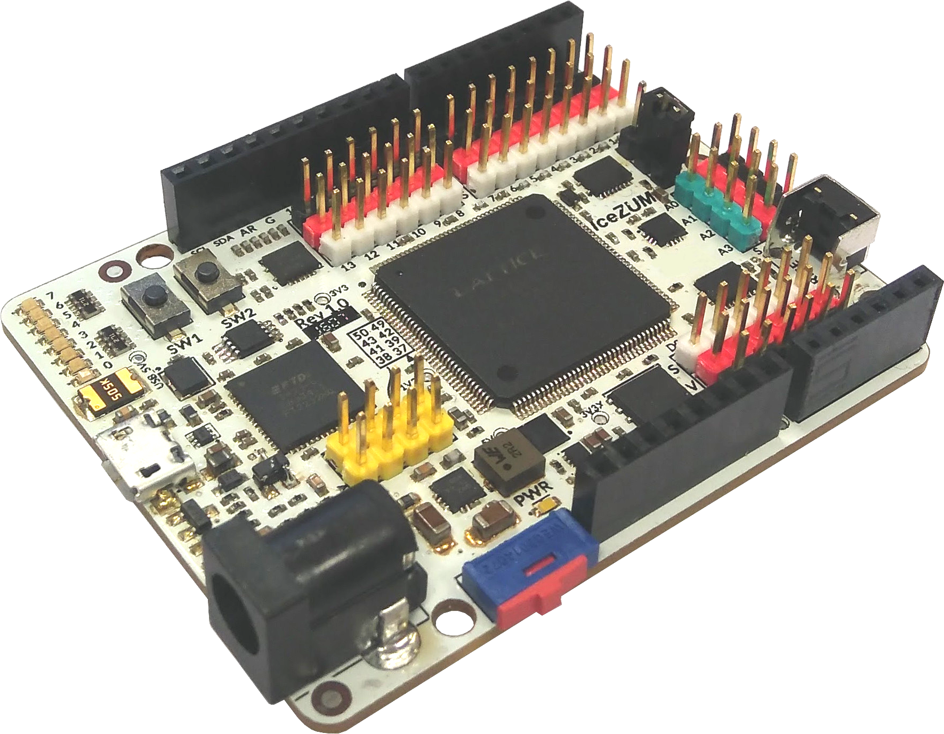
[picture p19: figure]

Figura 3.2: Icezum Alhambra. FPGA libre desarrollada con las estructura física de una placa Arduino [25].

La placa sigue el esquema de hardware y software libre promovido por Arduino. Su PCB y pinout siguen la misma estructura de éste por lo que es fácilmente compatible con una gran cantidad de electrónica acondicionada para el mundo Arduino e, incluso, compatible con sus Shields. Junto a la placa la comunidad está desarrollando tanto software gráfico, como Icestudio orientado a la creación y aprendizaje de circuitos electrónicos digitales mediante interfaz gráfica, como herramientas que faciliten la programación y carga del código descriptivo utilizado, integrándose en plataformas ampliamente utilizadas como PlatformIO.
Así pues, se pretende utilizar la Icezum Alhambra como sistema de bajo nivel, aportando, aprendiendo y contribuyendo en el proceso al conocimiento libre en el campo de las FPGAs y su uso en la robótica.
Mediante la utilización de un microordenador como la Raspberry PI como sistema de alto nivel, y el uso de una FPGA libre como la IceZum Alhambra para la implementación de los circuitos de bajo nivel, junto a la utilización de herramientas de prototipado rápido como la impresión 3D, se pretende la creación y experimentación con un sistema híbrido de control alto nivel-bajo nivel, fuertemente bioinspirado, que suponga una alternativa a otros medios de control tradicionales.

# Capítulo 4

# Método de evaluación

Para conseguir que el trabajo de fin de master cumpla los objetivos comentados en 1 y 3, se establecen los siguientes mecanismos para evaluar su avance y desarrollo.

## 4.1. Búsqueda de soluciones de locomoción en la Biorrobótica actual

Se propone la realización de un estado del arte que permita comprender el estado actual de la biorrobótica en el campo de la locomoción bionspirada, desarrollando un conocimiento sólido de la materia que permita implementar soluciones tanto dentro del propio proyecto, como de cara a desarrollos futuros. Para conseguirlo se realizará una lectura exhaustiva de la bibliografía existente así como la asistencia a conferencias y otros que traten la materia. Dado la gran cantidad de material existente en Internet e instituciones públicas, es posible llegar a un estado del arte apropiado sobre la materia.

## 4.2. Desarrollar una estructura de control Alto nivel-Bajo nivel

Para el desarrollo de la estructura de control Alto nivel-Bajo nivel propuesta en el trabajo, se utilizarán los medios descritos en el apartado de validación de la hipótesis 3, utilizando un microordenador como sistema de alto nivel y una FPGA para la construcción de los circuitos que actúen como bajo nivel. Para cumplir este objetivo, será necesario demostrar las principales diferencias del sistema propuesto respecto a otras estructuras de control, por lo que se deberán realizar pequeñas experimentaciones que comparen aspectos cuantitativos como el tiempo de respuesta ante un estímulo, la velocidad de ejecución, o la facilidad de control de la estructura de control propuesta frente a estructuras más tradicionales. Para ello se pueden utilizar pequeños robots simples, desde robots diferenciales a pequeños hexápodos u otros, que sean controlados con ambos sistemas. Dada la facilidad de crear este tipo de pequeños prototipos gracias a las impresoras 3D de bajo costo y electrónica simple

12

CAPÍTULO 4. METODO DE EVALUACI ´ | ON´ | 13

como la de Arduino, es posible realizar estos experimentos sin grandes dificultades, siendo además un paso fundamental para mejorar los conocimientos en la creación de los circuitos de la FPGA orientados al control robótico de bajo nivel que se aplicarán durante el proyecto.

## 4.3. Prototipo que implemente la hipótesis propuesta

Para demostrar que la estructura de control propuesta puede ser una alternativa real a otras estructuras de control, se diseñará, construirá y programará un prototipo de robot que utilice la estructura de control planteada. Dicho prototipo deberá tener las siguientes características:

Locomoción simultánea de varios grados de libertad: Dado que la estructura de control propuesta se basa en la ventaja que supone la velocidad de actuación de circuitos físicos frente a microprocesadores, así como su actuación en paralelo frente a la secuencial del microprocesador, estas características deberán ser clave en el prototipo desarrollado. Se propone un prototipo con múltiples grados de libertad en su locomoción que utilice patas o similares.

Bioinspirado: la hipótesis presentada se inspira en estructuras de control dadas en animales, lo que implica de por sí que el sistema sea bionspirado. Dado que se propone que el prototipo utilice patas, el paso natural es imitar una locomoción animal, e incluso sensorización y comportamiento, en el prototipo a realizar.

Modular y escalable: una de las principales ventajas que puede tener la utilización de una FPGA en vez de un microprocesador para el control de bajo nivel, es la posibilidad de actuación en paralelo de múltiples grados de libertad junto a sensores u otros, al poder almacenar la FPGA numerosos circuitos. Esta ventaja es muy relevante en sistemas con muchos grados de libertad, ya que los sistemas programados pueden ser lentos a la hora de gestionar dichos movimientos, mientras que su implementación por Hardware permite su funcionamiento de forma distribuida, en paralelo y escalable. Por ello se propone para validar la estructura de control, un prototipo con múltiples grados de libertad. Sin embargo esto implica limitaciones técnicas, como la capacidad de la FPGA a utilizar, o el número de entradas y salidas, así como de recursos, donde más grados de libertad implica normalmente más motores y más coste. Por dicha razón el prototipo a realizar deberá ser modular y escalable de forma que se pueda demostrar con las limitaciones existentes que la estructura de control planteada funcionaría igual si se aumentará en escala.

CAPÍTULO 4. METODO DE EVALUACI ´ | ON´ | 14

## 4.4. Mejora de la locomoción y otros sistemas mediante aprendizaje

Dado que el uso de FPGAs libres significa una mayor libertad en las herramientas de software utilizadas y al disponer de un microordenador como alto nivel, es posible experimentar con sistemas de aprendizaje sencillos capaces de modificar el código Verilog del sistema de bajo nivel, siendo capaz de cambiar y hacer evolucionar el equivalente al sistema nervioso central del robot, casi en tiempo real. Esto permite que el robot pueda adaptar su sistema de control ante situaciones o escenarios no conocidos, como aquellos con obstáculos más grandes cambiando de tipo de locomoción o de amplitud de zancadas, o ante imprevistos en su propio sistema tales como la rotura de una pata, pudiendo construir nuevos circuitos en tiempo real que le permita resincronizar el movimiento para mantener una correcta locomoción. La consecución de este objetivo implica la implementación de sistemas de aprendizaje usando, por ejemplo, librerías de inteligencia artificial en lenguajes como C++ o Python. Si bien es un objetivo ambicioso, es posible llegar a una implementación sencilla que sea fácilmente ampliable en futuros proyectos.

## 4.5. Implementación de CPG

Basándose en el estado del arte estudiado y las habilidades adquiridas en el diseño de circuitos en la FPGA, sería deseable la implementación y experimentación con CPGs dentro del proyecto. Debido a la dificultad que tiene el estudio e implementación de los CPGs, se propone la implementación de un sistema básico de osciladores mediante CPG que permita la ampliación futura del trabajo.

## 4.6. Documentación, colaboración y difusión

En primer lugar la memoria propia del trabajo de fin de máster deberá ser completa y bien estructurada, permitiendo ser un apoyo real a trabajos futuros del mismo campo. Dado que el proyecto se apoya en numerosas herramientas y comunidades Open Source, se pretende colaborar, difundir y aportar con los conocimientos adquiridos a los repositorios de dichas comunidades. Además, se utilizarán una serie de entradas en formato blog para divulgar, de manera no oficial y desenfada, la evolución del proyecto, así como las dificultades y curiosidades que implican la realización de un trabajo de fin de máster desde cero [26].

# Capítulo 5

# Conclusiones

El trabajo de la asignatura de Avances en Robótica presentado en este documento, tiene como objetivo el establecimiento de una hoja de ruta para la realización de un TFM fuertemente basado en el aprendizaje y la experimentación.
En una sociedad en la que las fronteras de los distintos campos de estudio son cada vez más difusas, la bioinspiración es hoy, más que nunca, un campo de estudio en el que desarrollar nuevas investigaciones para la resolución de viejos y nuevos problemas. En ese sentido, este trabajo ha presentado como el TFM ha realizar debe inspirarse en la naturaleza y los estudios previamente realizados en la biorrobótica para desarrollar una arquitectura de control híbrida y bionspirada que, aplicada a robots caminantes, permita desarrollar una alternativa a otros controles más tradicionales.
Para ello se plantea una estructura basada en el binomio Cerebro-Sistema nervioso periférico (SNP) que utilice como control de alto nivel un microprocesador que de ordenes a un control de bajo nivel desarrollado en hardware en vez de programación. Para ello se propone la utilización de FPGAs cuya principal ventaja es la velocidad de respuesta frente a un microprocesador a la hora de gestionar la locomoción de muchos grados de libertad de forma simultanea. El uso de FPGAs Open Source facilita el desarrollo de aplicaciones tales como la posibilidad de que el sistema de alto nivel reprograme el hardware del bajo nivel casi en tiempo real, aprendiendo y adaptándose a situaciones imprevistas sin perder su velocidad y flexibilidad.
La fuerte democratización de la tecnología ha permitido que hoy, más que nunca, sea abordable el estudio e investigación en el campo de la robótica de forma cada vez más práctica. El uso de hardware y software libre, sin ser una norma general, facilita en muchas ocasiones las tareas y el desarrollo de muchos estudios y aplicaciones sin disparar la cantidad y coste de los recursos utilizados. En este trabajo se han presentado diversas alternativas basadas en hardware y software libre como principales recursos para la creación de un prototipo de robot caminante con patas en el que se implemente la arquitectura a desarrollar.
Como conclusión, el trabajo aquí presentado es una investigación que sienta unas bases solidas para desarrollar el TFM planteado. Exponiendo sus principales hipótesis, campos de estudio, recursos disponibles, así como los criterios para probar dichas hipótesis y las posibles soluciones a los futuros problemas que puedan surgir. Siendo, por tanto, una guía fundamental que marcará el desarrollo del proyecto.

15

# Bibliografía

[1] “Los | héroes | robóticos | de | fukushima.” | http://www.xataka.com/
robotica-e-ia/los-heroes-roboticos-de-fukushima (http://www.xataka.com/robotica-e-ia/los-heroes-roboticos-de-fukushima) | (último | acceso:
Mayo 2016), Marzo 2015.
[2] “Darpa | robotics | challenge.” | http://www.darpa.mil/program/
darpa-robotics-challenge (http://www.darpa.mil/program/darpa-robotics-challenge) (último acceso: Mayo 2016), Junio 2015.
[3] “Unlucky robot gets stranded inside fukushima nuclear reactor, sends
back | critical | data.” | http://spectrum.ieee.org/automaton/robotics/
industrial-robots/robot-stranded-inside-fukushima-nuclear-reactor (http://spectrum.ieee.org/automaton/robotics/industrial-robots/robot-stranded-inside-fukushima-nuclear-reactor) (último acceso: Mayo 2016), Abril 2015.
[4] M. Raibert, K. Blankespoor, G. Nelson, R. Playter, and T. Team, “Bigdog, the rough-terrain quadruped robot,” in Proceedings of the 17th World Congress, vol. 17, pp. 10822–10825, 2008.
[5] M. Rubenstein, A. Cornejo, and R. Nagpal, “Programmable self-assembly in a thousand-robot swarm,” Science, vol. 345, no. 6198, pp. 795–799, 2014.
[6] “Fpgawars: Tools for exploring the open side of the fpgas.” https://github.com/FPGAwars (https://github.com/FPGAwars) (último acceso: Mayo 2016), Abril 2016.
[7] A. J. Gallagher, N. Hammerschlag, S. J. Cooke, D. P. Costa, and D. J. Irschick, “Evolutionary theory as a tool for predicting extinction risk,” Trends in ecology & evolution, vol. 30, no. 2, pp. 61–65, 2015.
[8] A. J. Ijspeert, A. Crespi, D. Ryczko, and J.-M. Cabelguen, “From swimming to walking with a salamander robot driven by a spinal cord model,” science, vol. 315, no. 5817, pp. 1416–1420, 2007.
[9] I. Delvolvé, T. Bem, and J.-M. Cabelguen, “Epaxial and limb muscle activity during swimming and terrestrial stepping in the adult newt, pleurodeles waltl,” Journal of Neurophysiology, vol. 78, no. 2, pp. 638–650, 1997.
[10] A. Sprwitz, A. Tuleu, M. Vespignani, M. Ajallooeian, E. Badri, and A. J. Ijspeert, “Towards dynamic trot gait locomotion: Design, control, and experiments with cheetah-cub, a compliant quadruped robot,” The International Journal of Robotics Research, vol. 32, no. 8, pp. 932–950, 2013.

16

[11] “Cheetah-cub robot mimics feline.” https://youtu.be/frTmPdNzVPI (último acceso: Junio 2016), Junio 2013.
[12] “Mit cheetah robot lands the running jump.” https://youtu.be/_luhn7TLfWU (último acceso: Junio 2016), Mayo 2015.
[13] “Kangaroo robot by festo.” https://youtu.be/_4luJ0ZSqy8 (último acceso: Junio 2016), Abril 2014.
[14] “Ls3-legged squad support systems.” http://www.bostondynamics.com/robot_ls3.html (http://www.bostondynamics.com/robot_ls3.html) (último acceso: Junio 2016), Junio 2016.
[15] J. Colorado Montaño, BaTboT: a biologically inspired flapping and morphing bat robot actuated by SMA-based artificial muscles. PhD thesis, Industriales, 2012.
[16] “Festo-bionicopter.” https://youtu.be/nj1yhz5io20 (último acceso: Junio 2016), Marzo 2013.
[17] “Smartbird-festo.” https://www.festo.com/group/en/cms/10238.htm (último acceso: Junio 2016), Enero 2012.
[18] “Festo-aquajelly.” https://youtu.be/N-O8-N71Qcw (último acceso: Junio 2016), Diciembre 2008.
[19] P. Phamduy, C. Milne, M. Leou, and M. Porfiri, “Interactive robotic fish: A tool for informal science learning and environmental awareness,” Robotics & Automation Magazine, IEEE, vol. 22, no. 4, pp. 90–95, 2015.
[20] “Diverbot underwater humanoid robot.” http://www.car.upm-csic.es/?portfolio=diverbot (http://www.car.upm-csic.es/?portfolio=diverbot) (último acceso: Junio 2016), Marzo 2013.
[21] M. Rubenstein, C. Ahler, and R. Nagpal, “Kilobot: A low cost scalable robot system for collective behaviors,” in Robotics and Automation (ICRA), 2012 IEEE International Conference on, pp. 3293–3298, IEEE, 2012.
[22] M. Dorigo, M. Birattari, C. Blum, M. Clerc, T. Stützle, and A. Winfield, Ant Colony Optimization and Swarm Intelligence: 6th International Conference, ANTS 2008, Brussels, Belgium, September 22-24, 2008, Proceedings, vol. 5217. Springer, 2008.
[23] P. Arena, “The central pattern generator: A paradigm for artificial locomotion,” Soft Computing, vol. 4, no. 4, pp. 251–266, 2000.
[24] “Project icestorm.” http://www.clifford.at/icestorm/ (último acceso: Junio 2016), Mayo 2015.
[25] “Icezum alhambra: an arduino/zum-like open fpga electronic board. synthesize hardware easily, using only open source tools.” https://github.com/FPGAwars/icezum (https://github.com/FPGAwars/icezum) (último acceso: Junio 2016), Junio 2016.

[26] “Diario de un tfm.” http://drmaker.es/category/tfm/ (último acceso: Junio 2016), Mayo 2016.
[27] A. J. Ijspeert, “Biorobotics: Using robots to emulate and investigate agile locomotion,” Science, vol. 346, no. 6206, pp. 196–203, 2014.
[28] A. J. Ijspeert, “Central pattern generators for locomotion control in animals and robots: a review,” Neural Networks, vol. 21, no. 4, pp. 642–653, 2008.
[29] M. Ambroise, T. Levi, S. Joucla, B. Yvert, and S. Saïghi, “Real-time biomimetic central pattern generators in an fpga for hybrid experiments,” Neuromorphic Engineering Systems and Applications, p. 134, 2015.
[30] “Auke ijspeert: Un robot que corre y nada como una salamandra.” https://www.ted.com/talks/auke_ijspeert_a_robot_that_runs_and_
swims_like_a_salamander?language=es#t-87728 (https://www.ted.com/talks/auke_ijspeert_a_robot_that_runs_and_swims_like_a_salamander?language=es) | (último | acceso: | Junio
2016), Diciembre 2015.

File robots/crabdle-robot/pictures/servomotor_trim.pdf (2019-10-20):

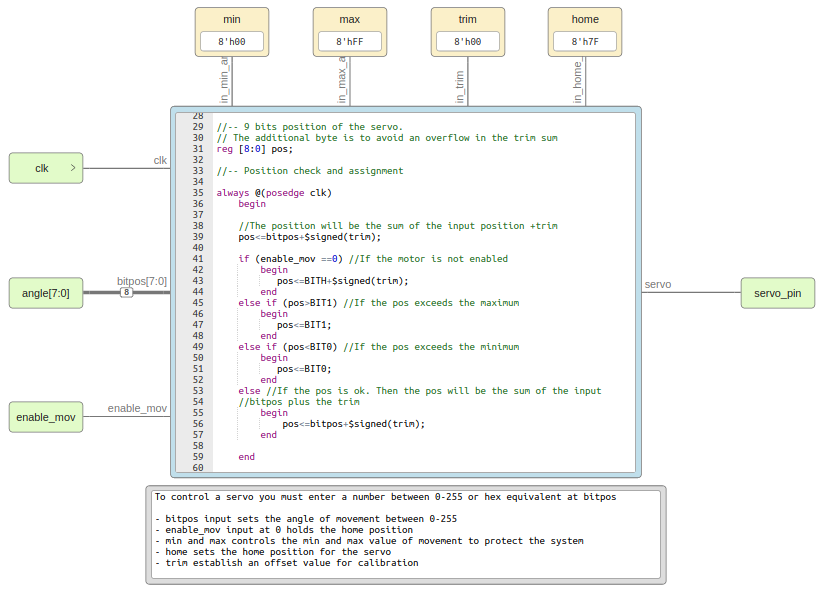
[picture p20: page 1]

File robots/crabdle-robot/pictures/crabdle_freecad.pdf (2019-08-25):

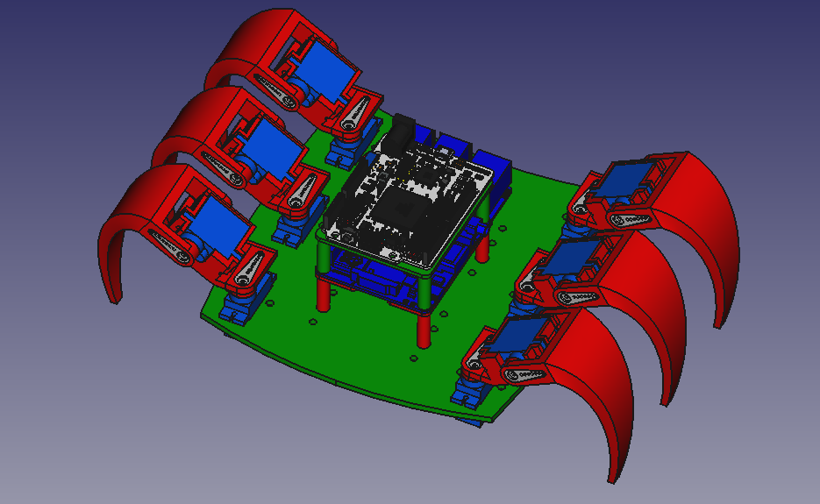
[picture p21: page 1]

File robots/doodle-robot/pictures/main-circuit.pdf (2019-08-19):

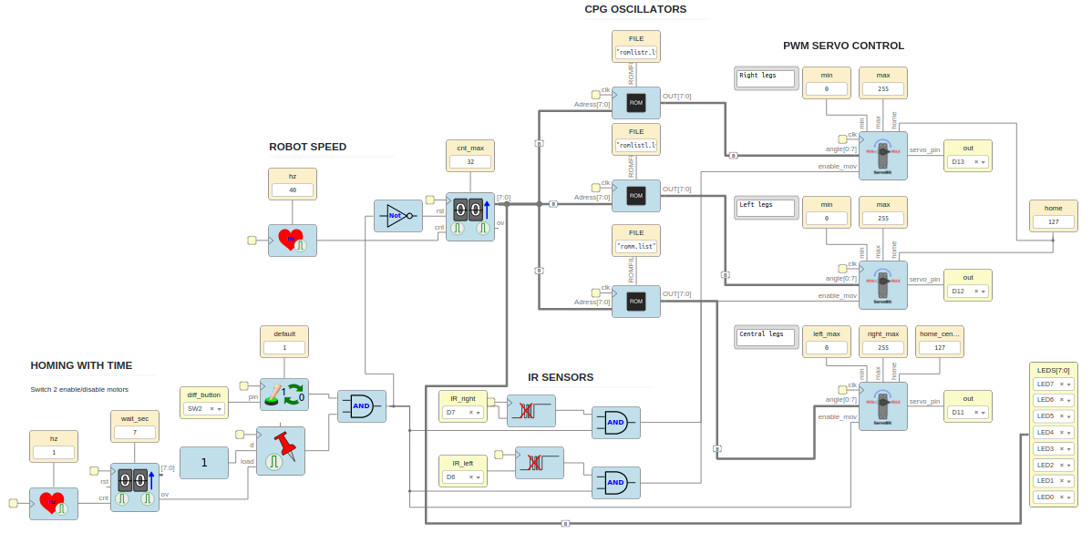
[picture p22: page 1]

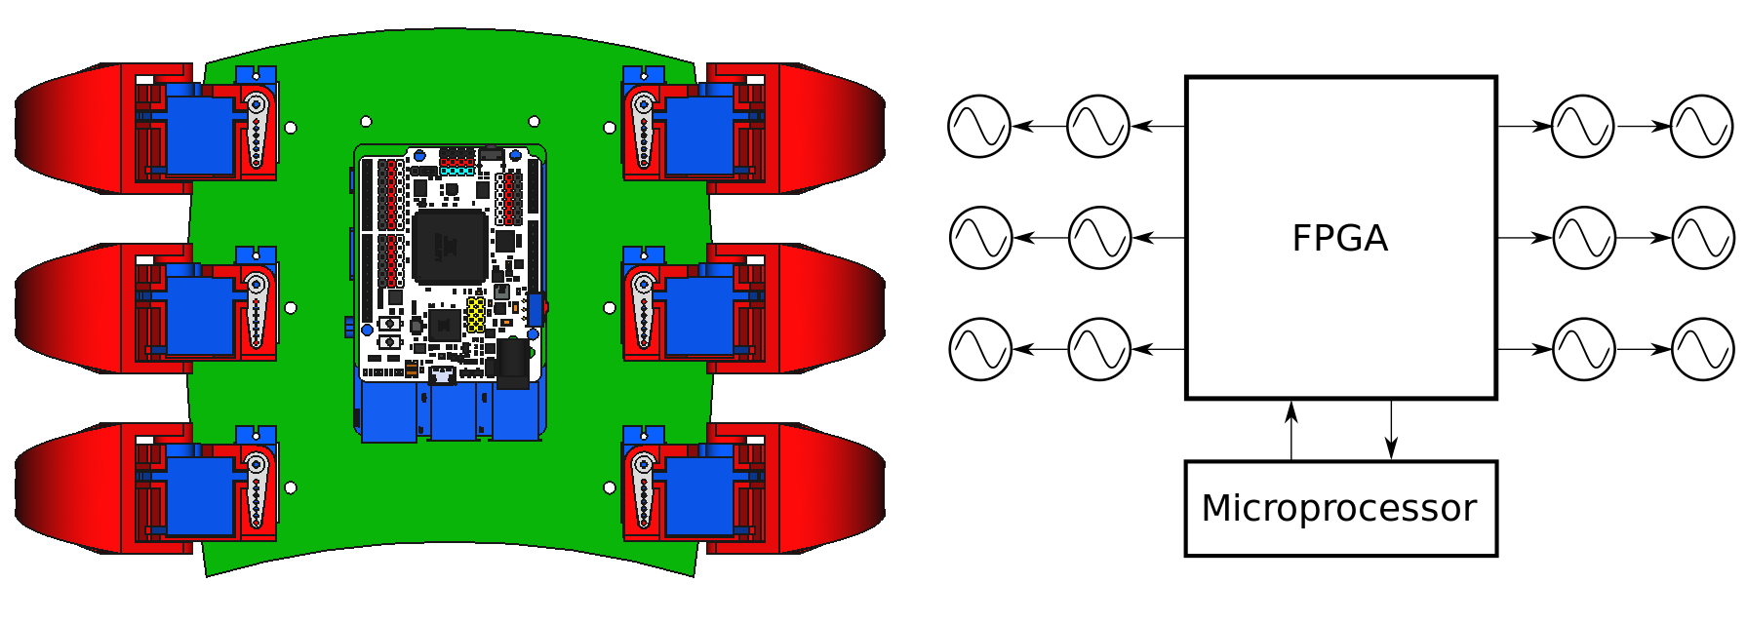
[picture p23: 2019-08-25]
robots/crabdle-robot/pictures/crabdle_architecture_diagram.png

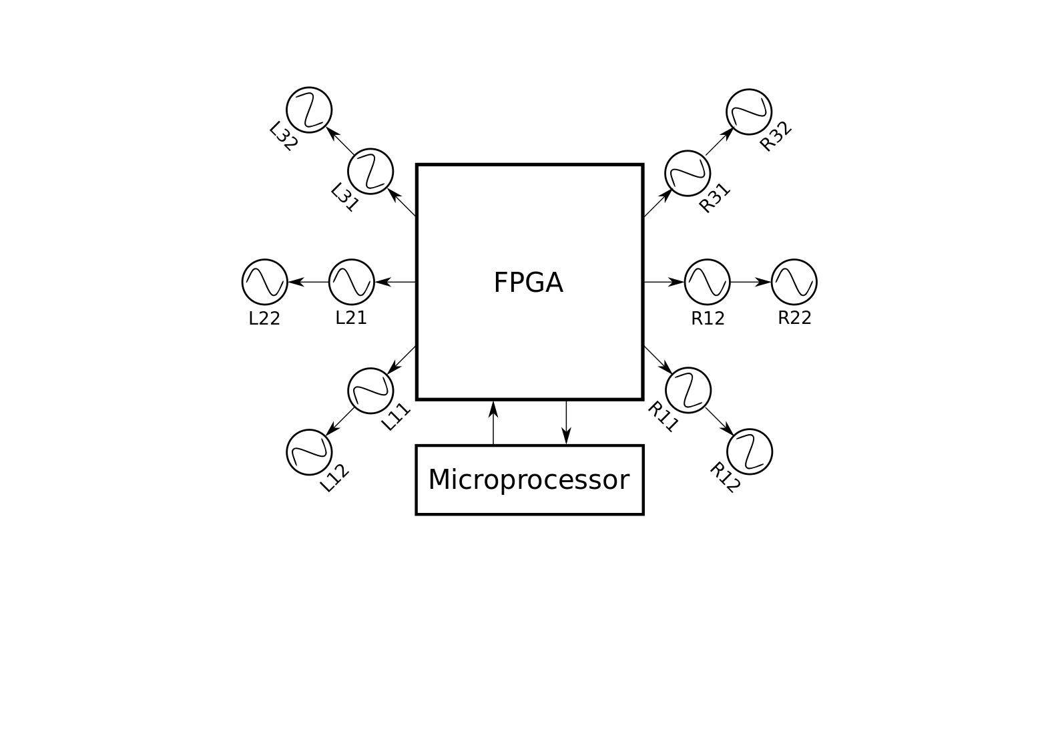
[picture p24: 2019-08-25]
robots/crabdle-robot/pictures/architecture_extended.png

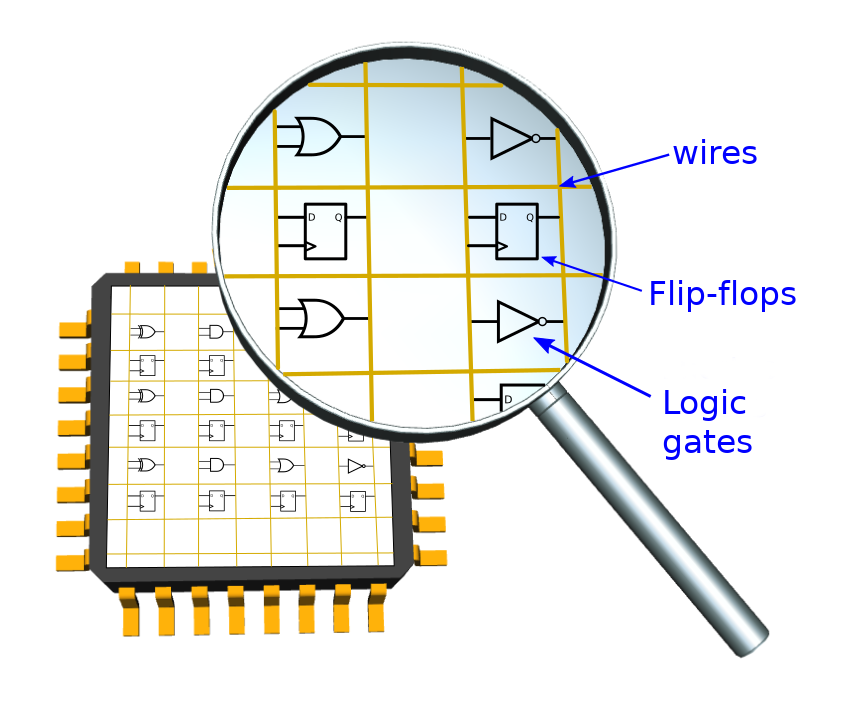
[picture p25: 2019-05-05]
Thesis Memory/pre-thesis-proposal/TFM Thesis document/figures/fpga_explaining-juan_gonzalez_gomez-cc-by-sa.png

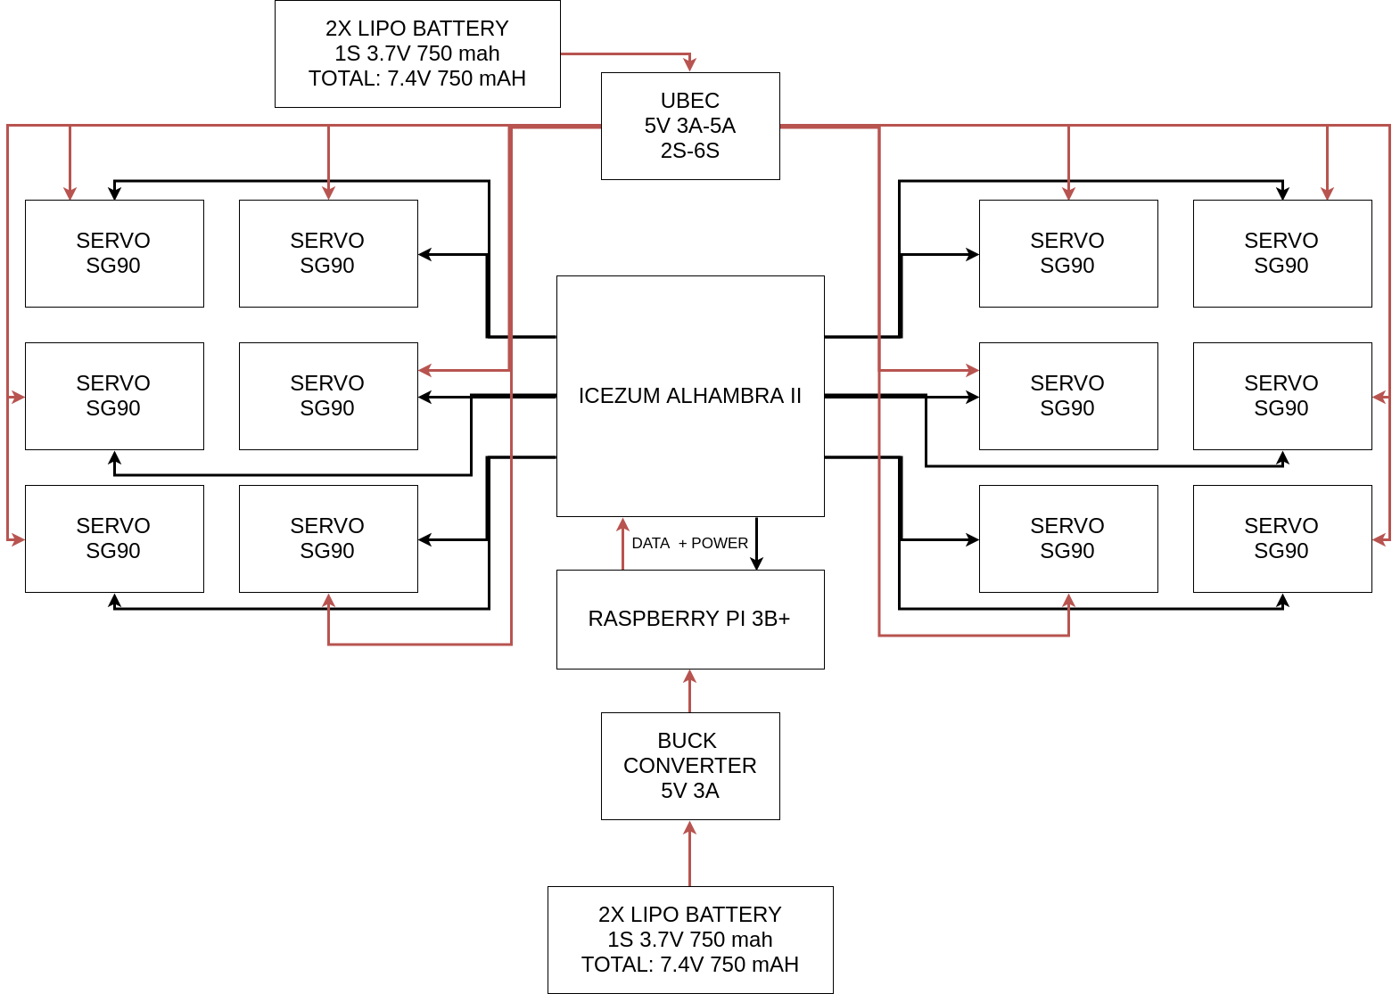
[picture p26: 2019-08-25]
robots/crabdle-robot/pictures/crabdle_electronics.png

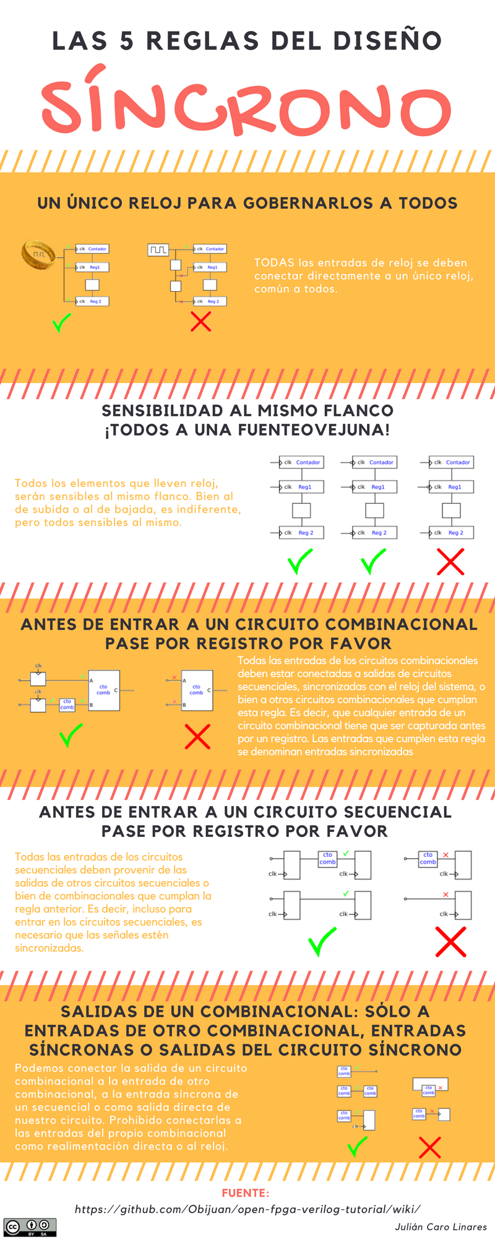
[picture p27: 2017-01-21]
Community_and_miscellany/infographics/Las cinco reglas del diseño sincrono/Las cinco reglas del diseño sincrono.png

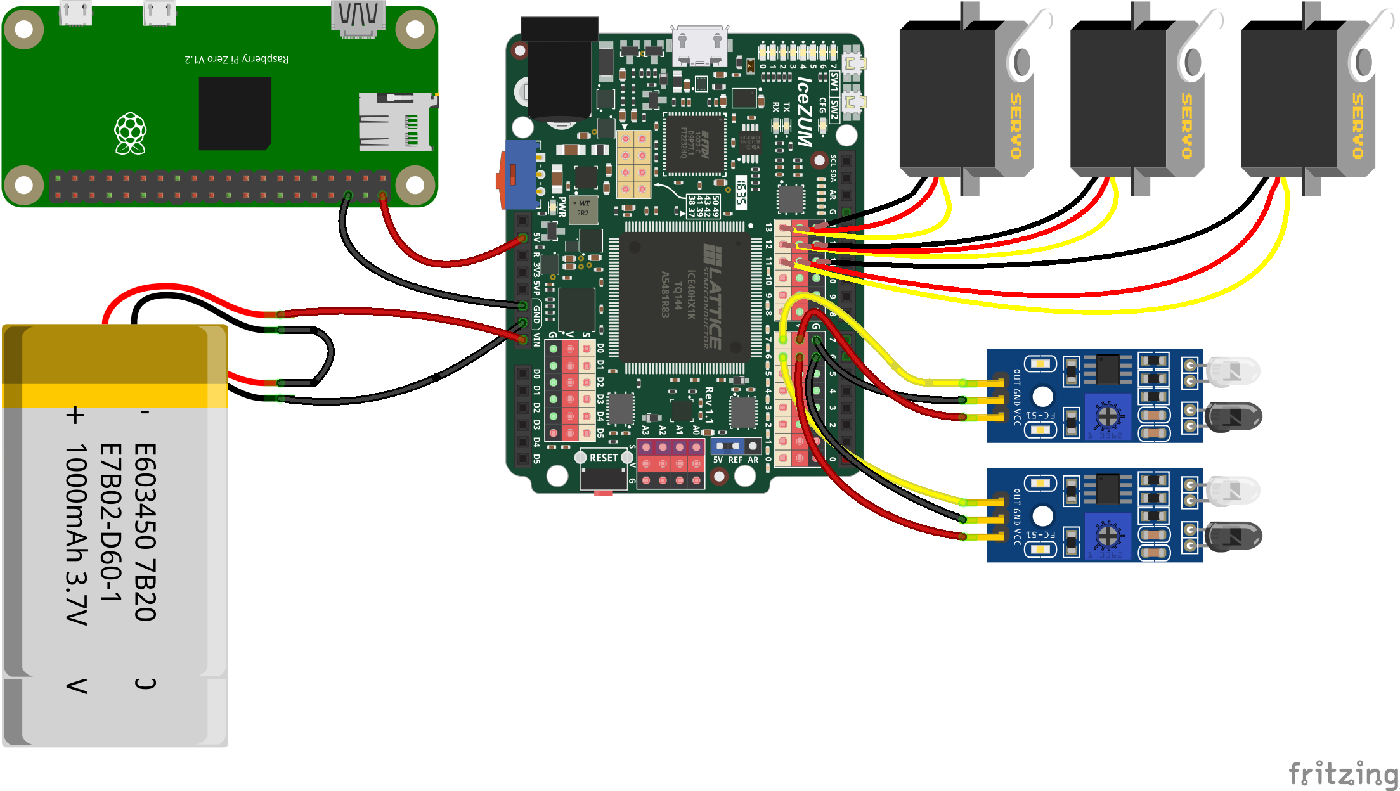
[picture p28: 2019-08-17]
robots/doodle-robot/fritzing/doodle_schematic_bb.png

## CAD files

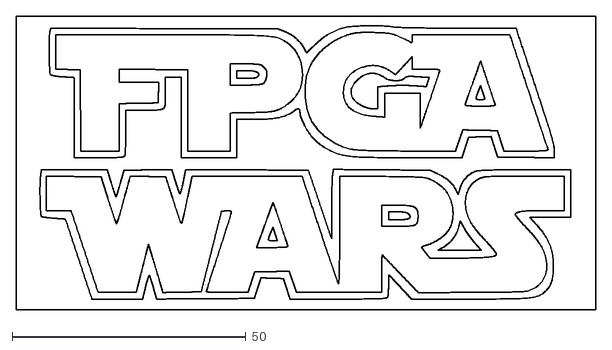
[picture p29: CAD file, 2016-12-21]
Community_and_miscellany/fpga-wars-alternative-logo-star-wars/src/fpgawarsstarwarslogo.dxf
123.9 x 62.7

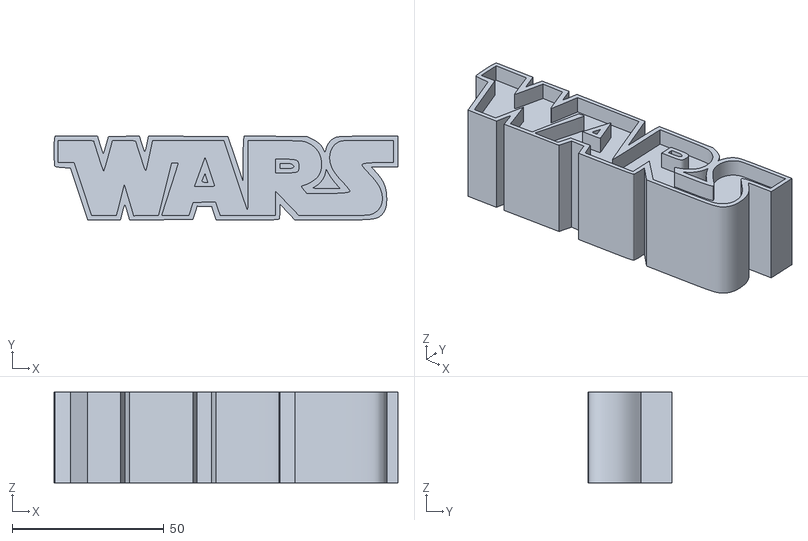
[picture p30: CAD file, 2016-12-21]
Community_and_miscellany/fpga-wars-alternative-logo-star-wars/stl/WARS.stl
113.4 x 27.7 x 30.0

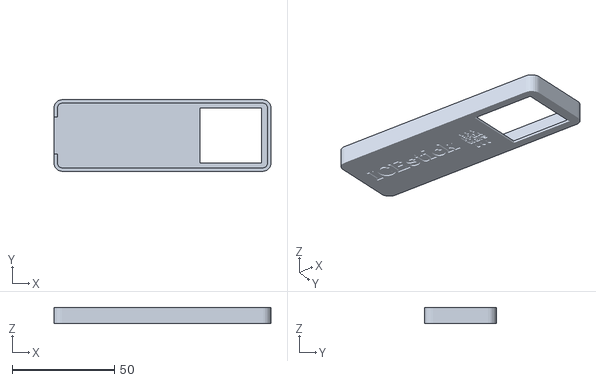
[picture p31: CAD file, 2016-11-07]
Community_and_miscellany/icestick-case/stl/icestick-case-logo_text_top.stl
106.0 x 35.0 x 8.00

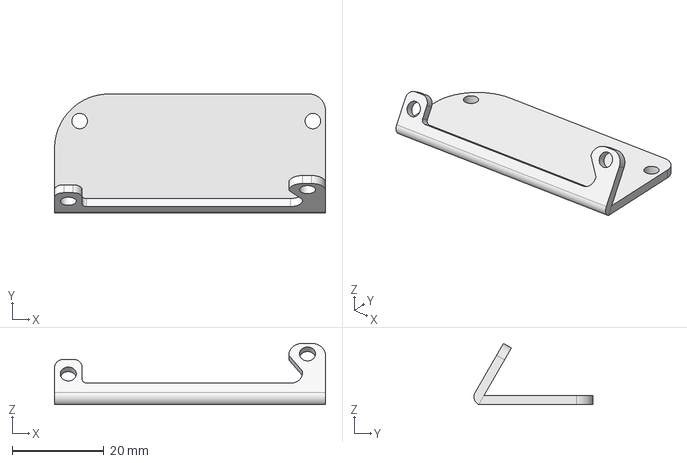
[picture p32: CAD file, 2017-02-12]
Community_and_miscellany/icezum-arduino-stand-holder/icezum-arduino-stand-holder.fcstd
59.0 x 25.9 x 13.3 mm

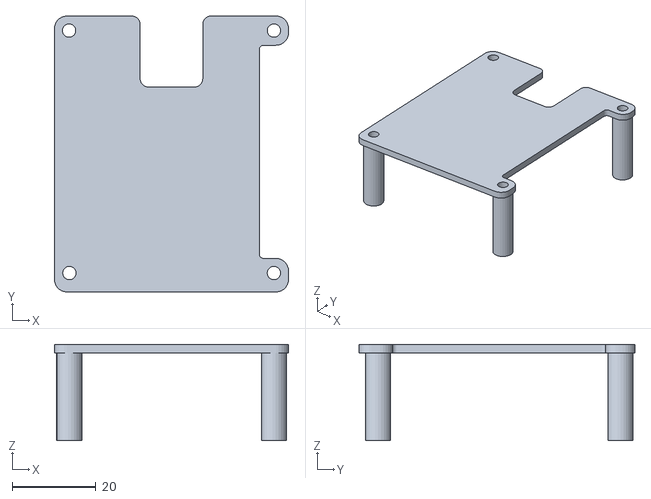
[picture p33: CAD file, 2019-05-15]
robots/crabdle-robot/3d-parts/stls/V3_electronics_holder.stl
56.0 x 66.0 x 23.0

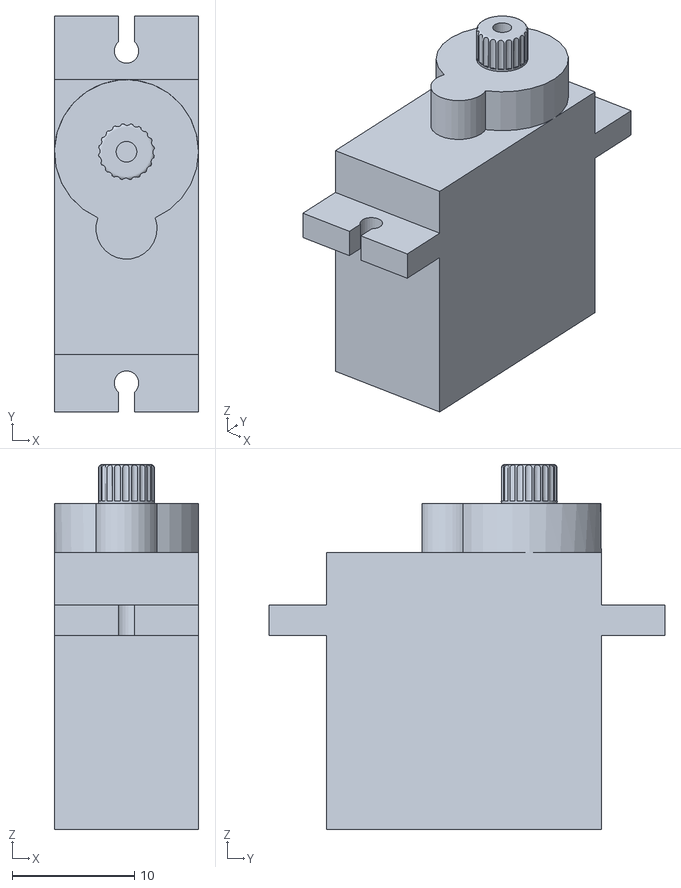
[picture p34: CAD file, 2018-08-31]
robots/doodle-robot/3d-parts/simulation_mesh/servo_central.obj
11.8 x 32.4 x 29.9

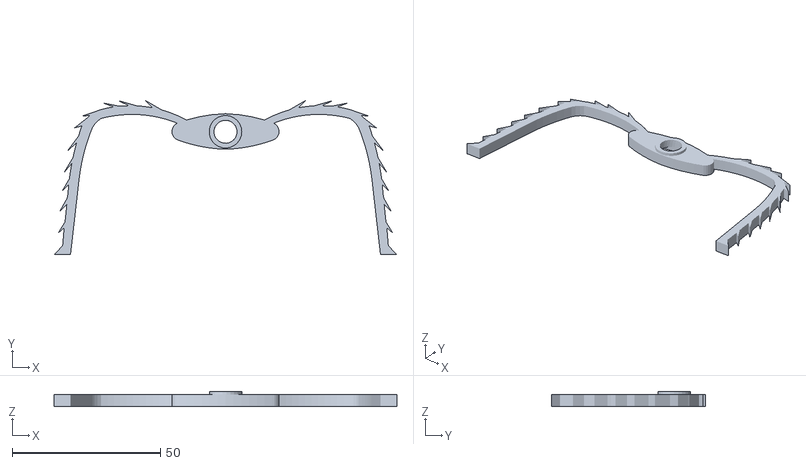
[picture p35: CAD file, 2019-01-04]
robots/doodle-robot/3d-parts/stl/central_leg_doodle_SG90.stl
115.8 x 52.1 x 5.00

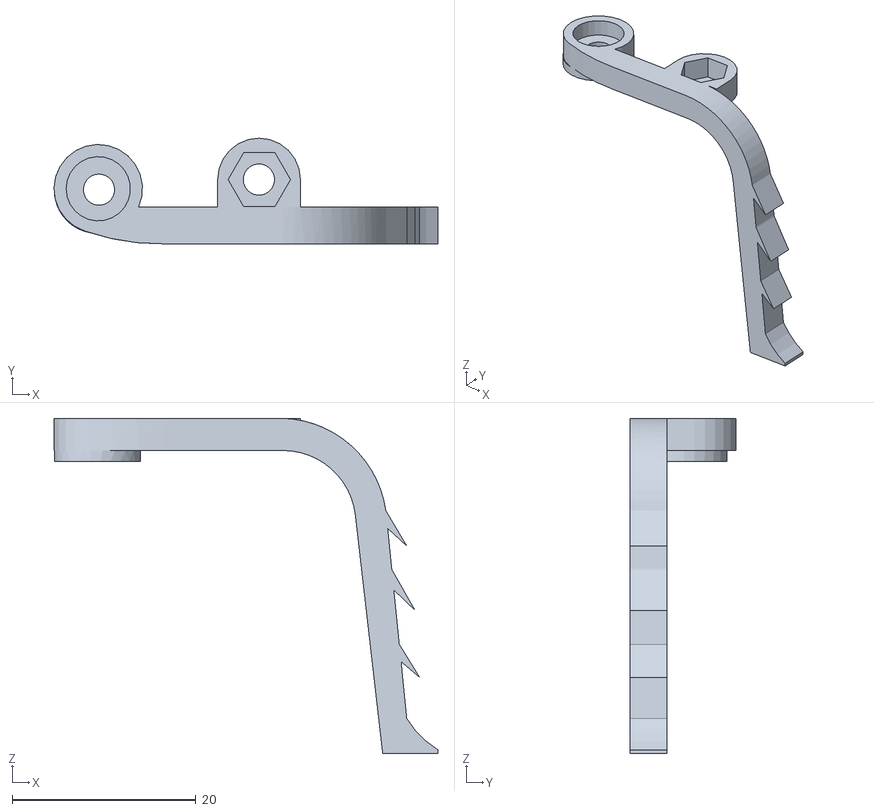
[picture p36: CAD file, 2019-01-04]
robots/doodle-robot/3d-parts/stl/SG92_legs/v2_front_left_leg_doodle.stl
41.8 x 11.5 x 36.5

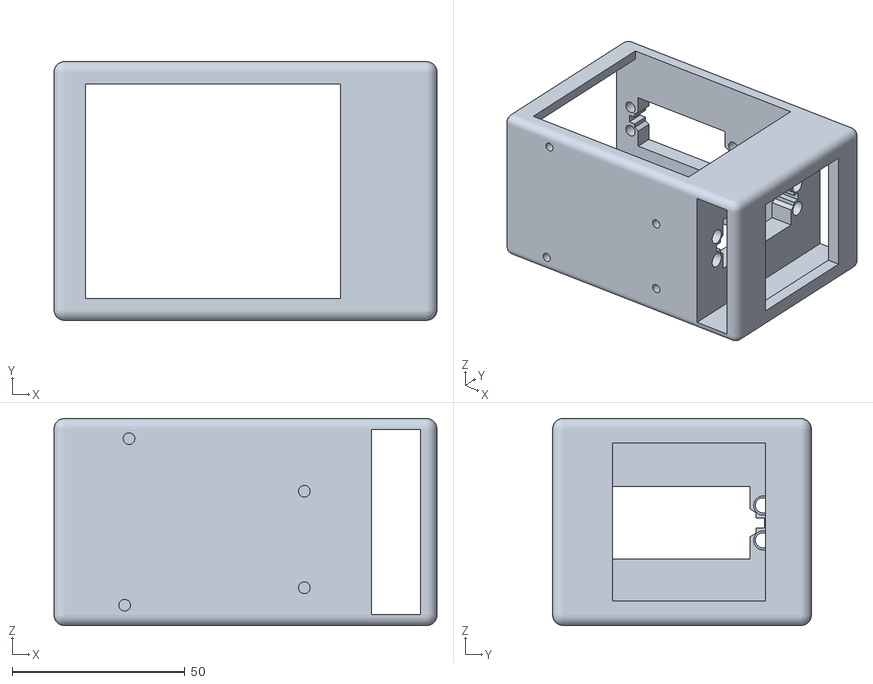
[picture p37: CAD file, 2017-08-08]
robots/randofo_robot_futaba_arduino_version/3D-Parts/stl/V3_randofo_robot_futaba_arduino_body.stl
111.0 x 75.0 x 60.0

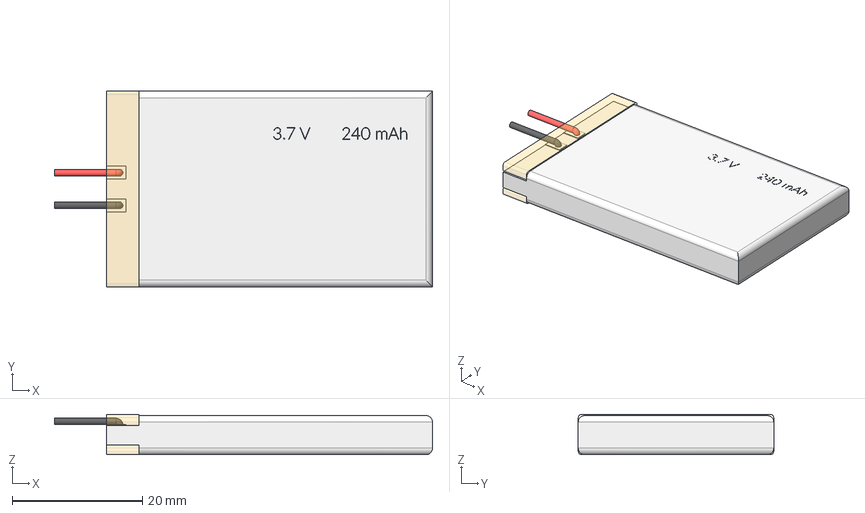
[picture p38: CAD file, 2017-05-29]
robots/resources/battery_lipo_3_7v_240mah.fcstd
58.0 x 30.0 x 6.20 mm
Clone of plus_wire
Clone of minus_wire
Clone of celonfan_rounded_2
Clone of data_text (2D)
Clone of battery_rounded
Clone of celofan_rounded

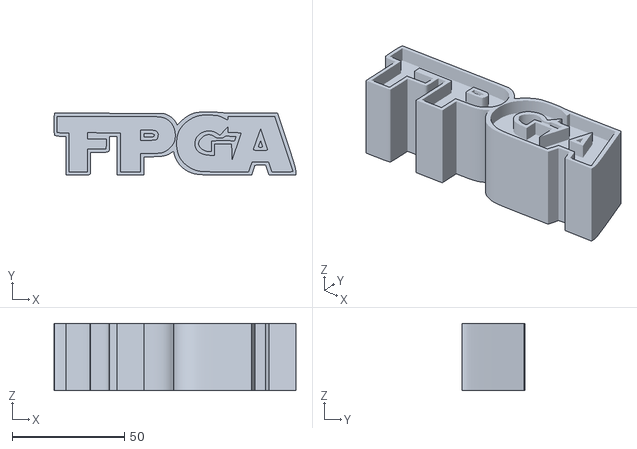
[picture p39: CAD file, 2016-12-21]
Community_and_miscellany/fpga-wars-alternative-logo-star-wars/stl/FPGA.stl
108.0 x 28.2 x 30.0

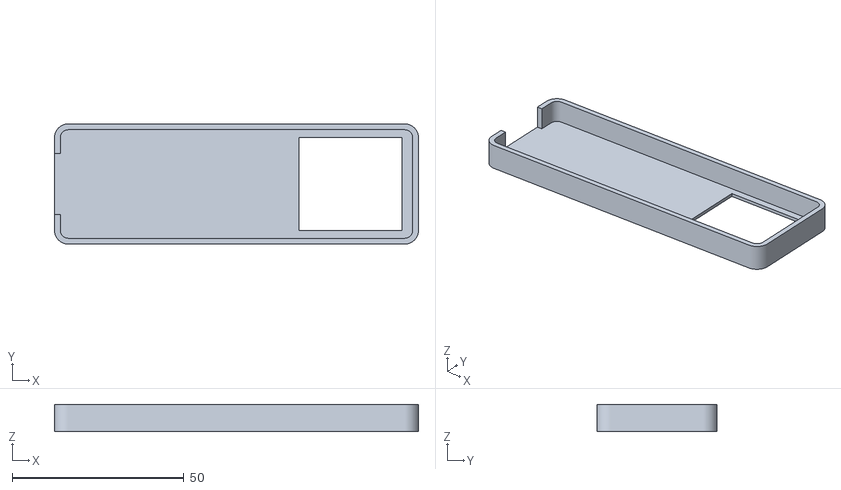
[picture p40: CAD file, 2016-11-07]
Community_and_miscellany/icestick-case/stl/icestick-case-bottom.stl
106.0 x 35.0 x 8.00

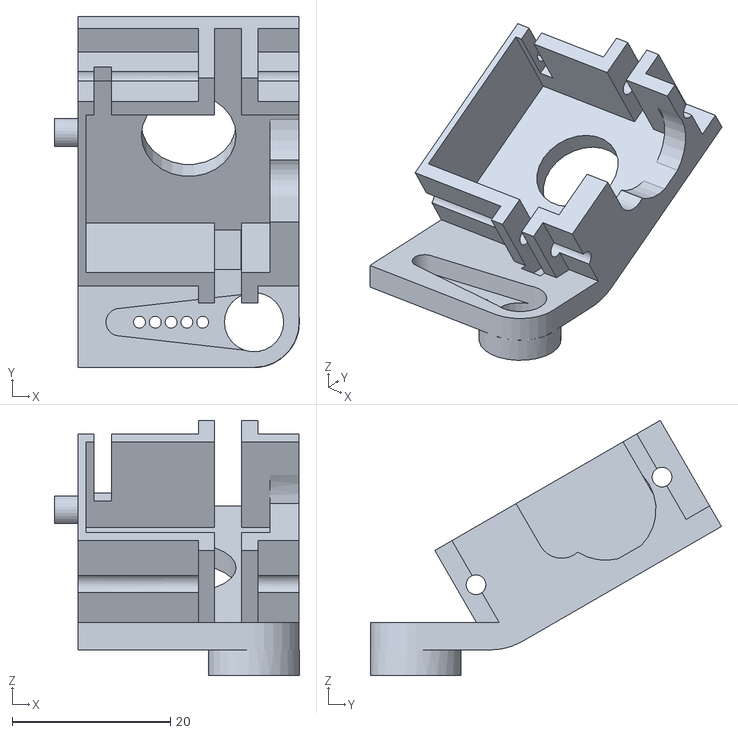
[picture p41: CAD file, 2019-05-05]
robots/crabdle-robot/3d-parts/stls/v9_q1_leg.stl
31.0 x 44.4 x 32.3

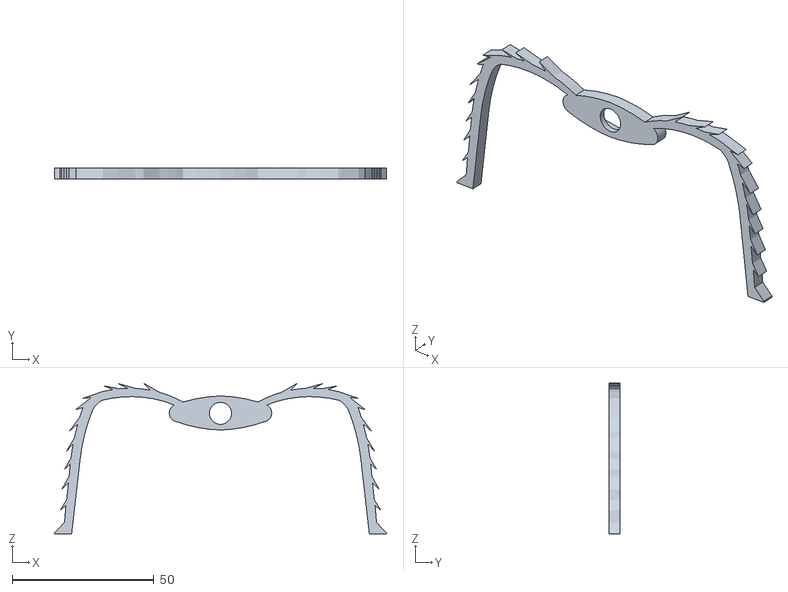
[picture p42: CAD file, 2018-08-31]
robots/doodle-robot/3d-parts/simulation_mesh/central_leg.obj
117.0 x 4.00 x 53.1

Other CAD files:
robots/final-prototype/final-prototype.fcstd
Community_and_miscellany/icezum-arduino-stand-holder/icezum_arduino_30_degrees_stand_holder.stl
robots/doodle-robot/3d-parts/stl/front_right_leg_doodle_SG90.stl
robots/doodle-robot/3d-parts/stl/SG92_legs/central_leg_doodle.stl
Community_and_miscellany/icestick-case/stl/icestick-case-screw-holes-bottom.stl
Community_and_miscellany/icestick-case/stl/icestick-plain_printing_plate.stl
Community_and_miscellany/icestick-case/stl/icestick-screw_logo_printing_plate.stl
Community_and_miscellany/icezum-arduino-stand-holder/icezum_arduino_vertical_horizontal_stand_holder.stl
robots/crabdle-robot/3d-parts/stls/V1_electronics_holder.stl
robots/crabdle-robot/3d-parts/stls/V2_electronics_holder.stl
robots/crabdle-robot/3d-parts/stls/V2_rasp-alhambra_holder.stl
robots/crabdle-robot/3d-parts/stls/V3_rasp-alhambra_holder.stl
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

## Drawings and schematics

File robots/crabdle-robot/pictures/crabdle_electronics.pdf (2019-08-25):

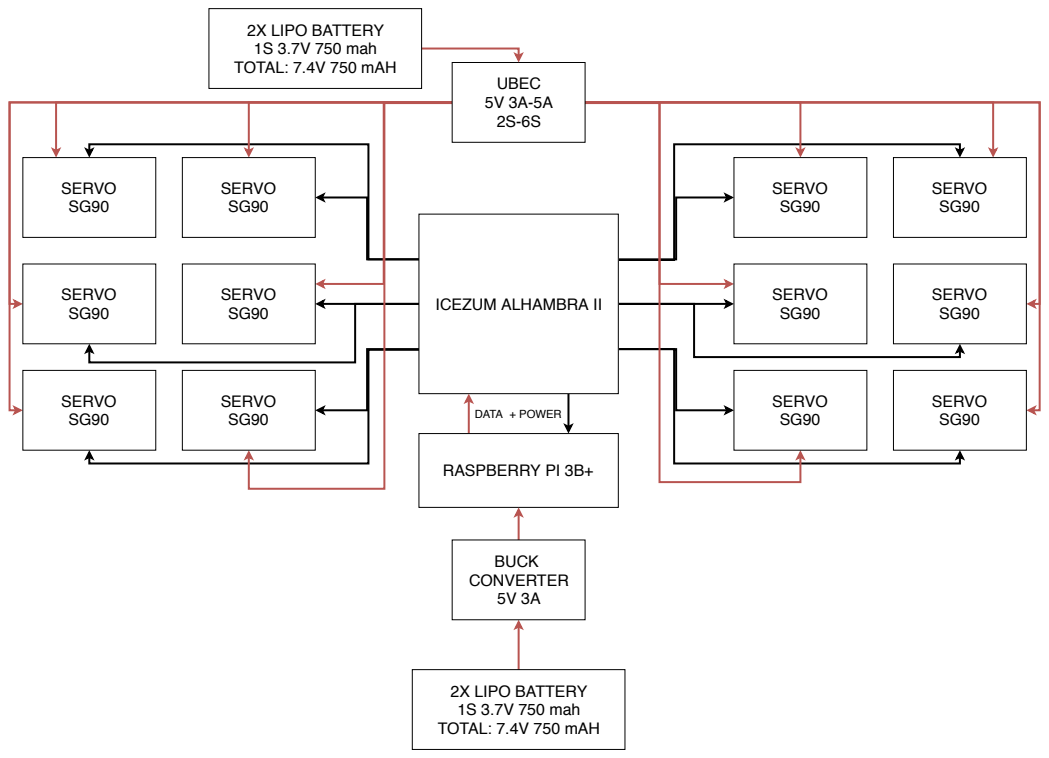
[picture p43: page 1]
RASPBERRY PI 3B+; DATA + POWER; 2X LIPO BATTERY 1S 3.7V 750 mah TOTAL: 7.4V 750 mAH; BUCK CONVERTER 5V 3A; UBEC 5V 3A-5A 2S-6S; SERVO SG90

ICEZUM ALHAMBRA II

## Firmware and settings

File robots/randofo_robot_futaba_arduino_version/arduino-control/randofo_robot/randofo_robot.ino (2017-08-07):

//
// Code for a 3D Printed Robot
// Learn more at: https://www.instructables.com/id/3D-Printed-Robot/
// This code is in the Public Domain
//


//add the servo library
#include <Servo.h> 

//Create two servo instances 
Servo myservo; 
Servo myservo1; 
 
//Change this numbers until the servos are centered!!!!
//In theory 90 is perfect center, but it is usually higher or lower.
int FrontBalanced = 75;
int BackCentered = 100;

//Variables to compensate for the back center of balance when the front shifts
int backRight = BackCentered - 20;
int backLeft = BackCentered + 20;



//Setup initial conditions of the Servos and wait 2 seconds
void setup() 
{ 
  myservo.attach(8); 
  myservo1.attach(9); 
  myservo1.write(FrontBalanced); 
  myservo.write(BackCentered);  
  delay(2000);
} 

 
 
void loop() 
{ 
  
  //Walk straight
  goStraight();
  for(int walk = 10 ; walk >= 0; walk -=1) { 
     walkOn();
  }   
 
  //Turn right
  goRight();
  for(int walk = 10 ; walk >= 0; walk -=1) { 
     walkOn();
  } 
  
  
  //Walk straight   
  goStraight();
  for(int walk = 10 ; walk >= 0; walk -=1) { 
     walkOn();
  }  
  
  //Turn left  
  goLeft();
  for(int walk = 10 ; walk >= 0; walk -=1) { 
     walkOn();
  } 

} 


//Walking function
void walkOn(){
    myservo.write(BackCentered + 30);
    delay(1000);
    myservo.write(BackCentered - 30);
    delay(1000);
}


//Turn left function
void goLeft(){
  BackCentered = backLeft;
  myservo1.write(FrontBalanced + 40);       
}


//Turn right function
void goRight(){
  BackCentered = backRight;
  myservo1.write(FrontBalanced - 40);              
}


//Go straight function
void goStraight(){
  BackCentered = 100;
  myservo1.write(FrontBalanced);             
}

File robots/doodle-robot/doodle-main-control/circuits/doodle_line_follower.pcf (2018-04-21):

set_io clk  21
set_io swh1  10
set_io swh2  11
set_io r_ir  112
set_io l_ir  113
set_io r_leg  144
set_io l_leg  143
set_io c_leg  142
set_io led[0]  95
set_io led[1]  96
set_io led[2]  97
set_io led[3]  98
set_io led[4]  99
set_io led[5]  101
set_io led[6]  102
set_io led[7]  104

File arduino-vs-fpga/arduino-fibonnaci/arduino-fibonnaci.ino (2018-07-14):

//Arduino fibonacci example from https://forum.arduino.cc/index.php?topic=112038.0

int ledr = 8;
int ledg = 3;

void setup()
{
 pinMode(ledr, OUTPUT);
 pinMode(ledg, OUTPUT);
 Serial.begin(9600); 
}

void loop()
{
 int n = 94;
 digitalWrite(ledr,LOW);
 digitalWrite(ledg, LOW);
 delay(2000);
 if(n==1||n==2)
 {
   digitalWrite(ledr,LOW);
   digitalWrite(ledg,LOW);
   delay(2000);
 }
 if(n>=3)
 {
   unsigned long long fib[n];
   fib[0] = 0;  // changed from 1
   fib[1] = 1;
   for(int i = 2; i<n; i++)
   {
     fib[i]=fib[i-2]+fib[i-1];
     char string[22];
     if(fib[i]/1000000000000000000ULL){
       unsigned long long temp = fib[i] % 1000000000000000000ULL;
       sprintf(string, "%lu", fib[i]/1000000000000000000ULL); 
       Serial.print(string);  
       sprintf(string, "%09lu", temp/1000000000UL); 
       Serial.print(string);  
       sprintf(string, "%09lu", fib[i]%1000000000UL); 
       Serial.println(string);
     } else if(fib[i]/1000000000UL){
       sprintf(string, "%lu", fib[i]/1000000000UL); 
       Serial.print(string);  
       sprintf(string, "%09lu", fib[i]%1000000000UL); 
       Serial.println(string);
     } else {
       sprintf(string, "%lu", fib[i]%1000000000UL); 
       Serial.println(string);
     }
   }
   digitalWrite(ledr,LOW);
   digitalWrite(ledg,HIGH);
   delay(5000);
 }
 digitalWrite(ledr,HIGH);
 digitalWrite(ledg,LOW);
 delay(2000);
}

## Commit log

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2016-11-07 Added a modified ICEstick case Obijuan design
    [icestick-case-bottom.stl, icestick-case-logo_text_top.stl, icestick-case-screw-holes-bottom.stl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]
2016-12-21 Aded miscelanous files
    [FPGA.stl, WARS.stl, fpgawarsstarwarslogo.dxf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]
2016-12-21 Files updated
    [icestick-case-bottom.stl, icestick-case-logo_text_top.stl, icestick-case-screw-holes-bottom.stl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]
2017-02-12 Added a Icezum ALhambra stand and the initial files for a simple hexapod robot
    [2051_servo_tower-pro-sg90.pk2.stl, icezum-arduino-stand-holder.fcstd, icezum.FCStd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]
2017-02-22 one new day
    [V3_leg_hole.stl, solid_v1_hexapod_leg.stl, v1_hexapod_leg.stl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]
2017-03-01 Freecad files and some others stl test updated
    [base_first_try.stl, non_servo_leg.stl]
2017-03-06 Small improvements in the base design, added first leg link version
    [V1_leg_link.stl]
2017-03-08 Central leg designed
    [V1_central_leg.stl]
2017-03-12 Demos folder added again and new Hexapod base version
    [V2_base.stl, V2_central_leg.stl, V3_base.stl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]
2017-03-16 Robot updated
    [insect_base.stl, insect_link.stl, leg_insect_back_left.stl]
2017-03-25 New robot base prototype+Some tries in the servo PWM control with a ROM
    [V4_base.stl]
2017-03-27 Experimental board holders
    [quick_adapter.stl]
2017-03-28 New base version added
    [prueba.stl]
2017-03-29 New version of non servo leg with a hole nut
    [v4_prueba_leg_non_servo_nut.stl, v4_try_leg_non_servo.stl]
2017-04-02 New front leg with nut version added
    [V4_leg_insect_nut.stl]
2017-04-02 New leg chain created
    [new_front_servo.stl, new_leg_chain.stl, new_servo_right.stl]
2017-04-03 Legs with nuts holes done
    [leg_Try.stl, leg_more_nut_space.stl, prueba_leg_wide_nut.stl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]
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2017-04-26 Alternative designs to the base
    [V5_base_alt_design.stl]
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2017-05-25 Battery model and first battery holder added
    [battery_3_7v_240_mAh.obj, battery_3_7v_240mAh.step, battery_holder.stl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]
2017-05-28 Final battery box added
    [V2_battery_holder.stl, V6_base.stl]
2017-05-29 Folder cleaned- Working on cad doodle-robot details
    [V1_central_leg.stl, V1_leg_link.stl, V2_base.stl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]
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2017-06-05 Added doodle_robot stl files
    [back_left_leg_doodle.stl, back_right_leg_doodle.stl, base_doodle.stl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]
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2017-07-01 Doing the oscillator servo controller
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2017-07-10 Romlists generator improved-Icestudio oscillator servo improved with min and max values
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2017-08-08 Readme updated. Randofo body rotated for a better printing
    [V3_randofo_robot_futaba_arduino_body.stl]
2017-09-19 fixin small errors
    [V2_randofo_robot_futaba_body.stl, V3_randofo_robot_futaba_arduino_body.stl, back_left_leg_doodle.stl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]
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2017-10-04 New doodle base compatible with raspy zero created
    [base_doodle_raspbzero.stl]
2017-10-12 Added a small buzzer options inside the advaced line follower
    [default.cfg]
2017-10-12 Central support servo base translated
    [base_doodle_raspbzero_central_motorback.stl]
2017-10-12 Some errors fixed
    [base_doodle_raspbzero_central_motorback.stl]
2017-10-17 Stls changes in doodle robot
    [V1_base_doodle.stl, V2_base_doodle.stl, V3_base_doodle.stl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]
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2018-07-14 Added Fibonacci to stress the Arduino oscillators movements
    [arduino-fibonnaci.ino]
2018-08-11 Structure of the final robot added.
    [final-prototype.fcstd]
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2018-08-28 Raspy and alhmabra holder in progress
    [rasp-alhambra_holder.stl]
2018-08-28 V2 of the adapter ready
    [V2_rasp-alhambra_holder.stl]
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2018-09-09 New iteration of the electronics holder. Holes in the base created
    [V2_electronics_holder.stl]
2018-10-03 new IROS 2018 demo
    [V1_electronics_holder.stl, V2_electronics_holder.stl, V2_rasp-alhambra_holder.stl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]
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2018-11-03 Added square signals to oscillator rom generator, added calibrationservos icestudio program
2018-11-04 Lot of doodle programs for the workshop updated
    [data_x_x2_x3.csv, demodata.csv, msft.csv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]
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2018-12-02 Old doodle main part removed
    [V3_base_doodle.stl, doodle_main_parts.stl]
2018-12-02 Doodle main parts with new base added
    [doodle_main_parts.stl]
2018-12-27 WIP Q1 Leg basic horn base
    [q1_basic_base_horn_test.stl]
2018-12-31 Servo to 30 degrees, test q1 leg
    [q1-concept-tray.stl, v1_q1_basic_base_horn_test.stl, v2_q1_basic_base_horn_test.stl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]
2019-01-03 Q! leg base WIP
    [v0-q2-bed.stl]
2019-01-03 Doodle base improvemente. Pillars more resistant
    [V4_base_doodle.stl]
2019-01-03 SG90 horn leg done
    [back_left_SG90_leg_doodle.stl, back_right_SG90_leg_doodle.stl]
2019-01-03 Lot of base changes
    [V4_base_doodle.stl]
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2019-01-04 New legs for the cheap SG90 horns servomotors
    [V3_base_doodle.stl, V4_base_doodle.stl, back_left_leg_doodle.stl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]
2019-01-04 New SG90 and SG92 front legs
    [v2_front_left_leg_doodle.stl, v2_front_left_leg_doodle_SG90.stl, v2_front_right_leg_doodle_SG90.stl]
2019-01-04 Doodle SG90 version done
    [back_left_SG90_leg_doodle.stl, back_right_SG90_leg_doodle.stl, central_leg_doodle_SG90.stl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]
2019-01-04 old doodle parts removed
    [doodle_main_parts.stl]
2019-01-04 SG90 Doodle version improved
    [V4_base_doodle.stl]
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2019-05-05 Added some stl and images
    [v8_q1_leg.stl, v9_q1_leg.stl, v9_q1_leg_right.stl]
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2019-05-15 New rapspy holder to keep the batteries under it. WIP basic hexapod behaviour
    [V3_electronics_holder.stl]
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2019-08-19 Final protoype folder cleaned
    [V1_electronics_holder.stl, V2_electronics_holder.stl, V2_rasp-alhambra_holder.stl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]
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2019-08-21 Name for the final prototype defined: Crabdle
    [V1_electronics_holder.stl, V2_electronics_holder.stl, V2_rasp-alhambra_holder.stl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]
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2020-07-25 Cleaning. .gitignore added. test-apio removed
    [default.cfg]
2020-08-01 FPGA Wars Alternative logo Fixed- EN Readme added
    [FPGA.stl, WARS.stl, fpgawarsstarwarslogo.dxf]
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
